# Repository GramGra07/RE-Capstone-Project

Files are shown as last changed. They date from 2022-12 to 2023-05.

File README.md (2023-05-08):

# Programmable, Autonomous Car
## Zale Diawara and Graden Gentry
## 5/6/23

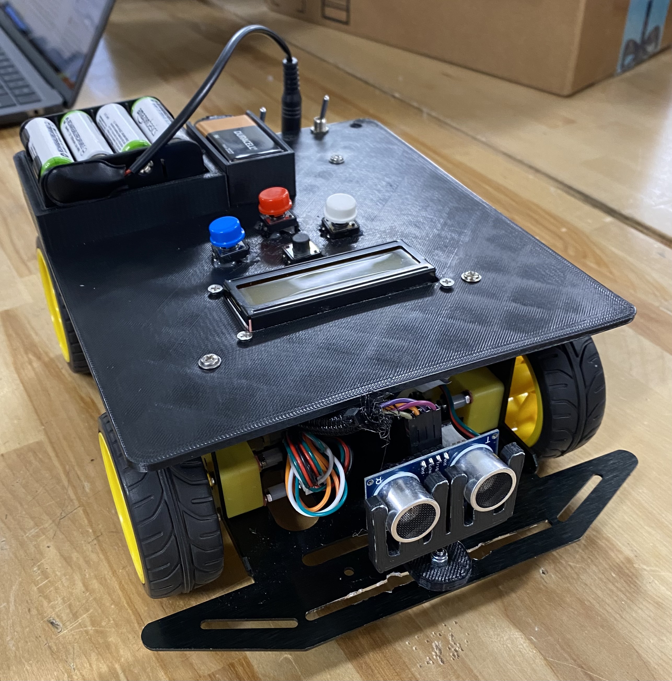
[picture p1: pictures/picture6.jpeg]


 ## Design Summary

We have made a robotic car that will allow a user to set direction and distance instructions for the robot to follow. For instance, the user will start the car and the LCD display will ask for a direction which will be input using one of the three buttons ( black, white, blue). It will then put the current selection on the LCD display. If the user is satisfied with their selection, they will tap the red button to accept the response and it will move on to selecting a distance. A base distance will be already selected and the user will use the white and blue buttons to change the distance. It will only allow the user to select 0 cm if the user has previously selected a direction of right or left. If the user selects forward, the minimum distance is 20 cm and the maximum is 90 cm. Once the user is again satisfied with the selection they will tap the red button again and it will save the selection. At this point in the program, it will allow the user to do the process again, or run the robot by pressing the red button again. Once running, the car will make sure it doesn’t crash by using a distance sensor to stop it an average of 6 cm away from an object.

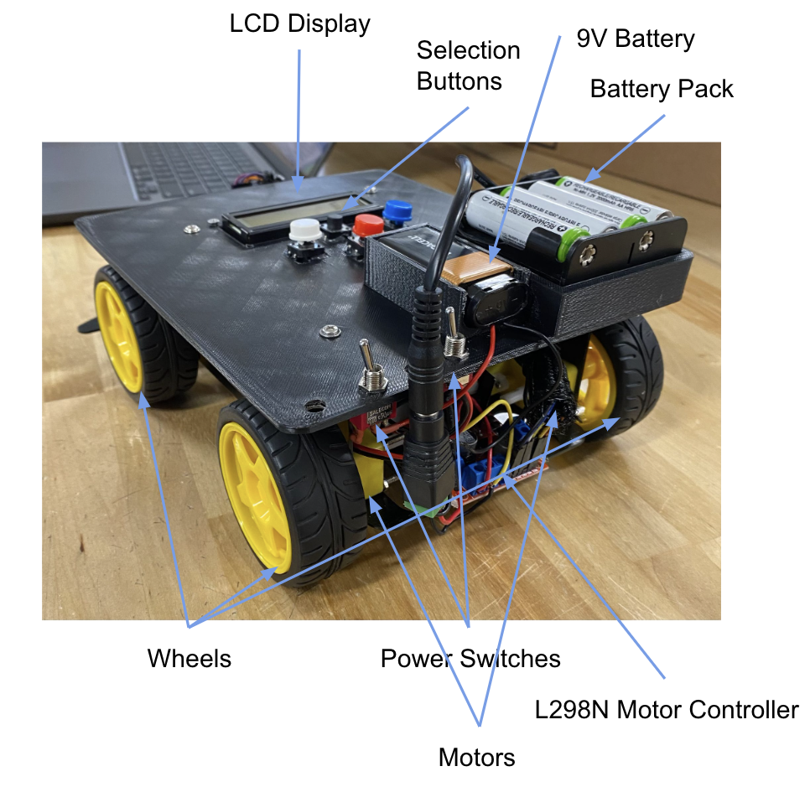
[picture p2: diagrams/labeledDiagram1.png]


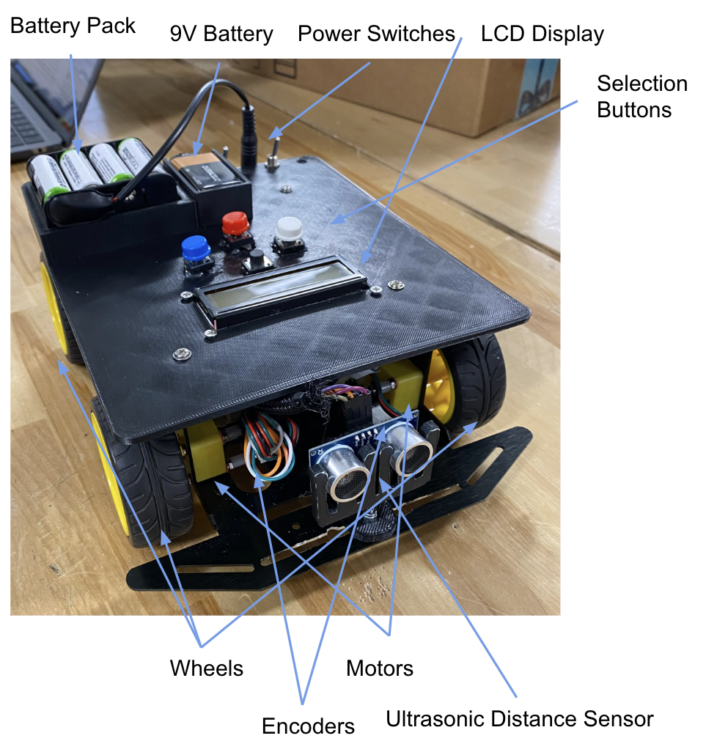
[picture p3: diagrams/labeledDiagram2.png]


## System Details

The robot is using some basic parts like Arduino motors and more complex parts like the Arduino Mega Elegoo. The first element of the robot where everything starts is the Arduino Elegoo because that is where the code is stored and also it is the part that sends those codes to the motors, the buttons and the LCD screen. The Arduino Elegoo Mega is the communicator between the buttons and the motors to transmit the instructions from the buttons to the motors, between the buttons and the LCD screen to display the instructions given from the buttons and finally between the motors (especially the encoders) and the ultrasonic sensor to tell the motors to stop when the robot is too close to hit something (around 6 cm). 
All these parts need power to run. At the beginning we used a battery pack with eight rechargeable small batteries with 1.2V and 2000mAh each to power both the Arduino and motors but we found that it wasn’t enough to power both. Because of this we use eight rechargeable batteries to power the motors, and a 9V battery to power the Arduino  (Figure 3). 
The robot also needs a lot of code in order to run correctly and efficiently. We use two true and false encoders to determine position and are able to count encoder ticks. After the robot is started, the user will allow the robot to calibrate, and manual calibrate if needed, and then will push the red button to start the program. Then they will start creating instructions for the robot by selecting a direction and distance for each step as seen in Figure 2. Our wiring is fairly simple. We have a breadboard in the middle for power and ground that most things are plugged into. Through this, we are able to get many more slots for power and ground and it is easier to distribute power. Most of our wires are organized through zip ties and cable holders. You can see the wiring diagram in Figure 1. There are a lot of wires that we have to manage and contain. We are using a lot of the pins on our Arduino Mega, which was the entire point of getting it. We have put hot glue on most of the connections to the Arduino to make sure they stay connected.
The code is based on functions and is all linear. There is no code in the loop() section that Arduino gives you because this would result in a repetition of the code we want to run only once. To start, it runs the selection code, found in Code Block 1, and then will break out of that once it is told to run. This will repeatedly ask the user for two inputs, a direction and distance until the user decides to run the program. Then, it will run the code to make the motors run until the encoders count to a certain number based on the instructions the user has given. This code is found in Code Block 3. We have also created functions to run the LCD. These are able to cut the message that the LCD will use because the LCD is only 16 characters long. The print function, found in Code Block 2, checks that the message variable is less than the 16 character limit, but if it is more than 16 characters it will cut the message down and make a second message for the second line. We also ran into a problem with the true and false encoders, if one is true and the other is false, the one that is false will go farther than the one that is true. To solve this problem, we calibrate the encoders and motors through the functions in Code Block 4, which contains both automatic and manual calibration options. The automatic function works by making the motors stop when both encoders are false. The manual function will tell the user the current encoder values and finish once both are at the correct position.
We 3D printed two parts, the top of the robot and the 9V battery holder found in Figure 4 and 5 in the appendix. 3D printing was very useful because it allowed us to accurately manufacture parts that we needed. We used the top of the robot print to mount the LCD, buttons, switches, and batteries. We printed the 9V battery holder and attached it to the top of robot part.
There are not many mechanical aspects to this project but we have used the Spartan kit as a base. Our current drivetrain has four Arduino motors mounted to a metal frame from the Spartan kit. Two of these motors have encoder mounts built in. Mostly because it already had everything we needed so we could start testing immediately. There are special mounts for the encoders on the motors, and convenient spots to mount the motors. There are four beams that go straight up to attach the top of the robot to the bottom frame. Inside the frame, there is enough space for the Arduino, motor controller, and motors inside the robot.

## Design Evaluation

While building this robot, we have incorporated a LCD screen as an output display, four buttons for user input, a distance sensor and encoders for autonomous input, four reversible DC motors using a L289N motor driver, and a lot of programmed logic in the software. The programmed logic includes our algorithm that indexes through the variable called actions and tells the robot what to do, found in Code Block 5, and our logic that instructs the robot to run the LCD screen. Refer to Code Block 2 for more details on running the LCD screen. We have made every effort to make sure every connection is solid by hot gluing and soldering the wires and that there are no exposed wires that could cause harm. We have two switches that control power to the motors and the Arduino. If either switch is flipped off while the robot is driving, it will stop. Our cost was around $70, mostly used by the Arduino Spartan kit we used as our base. We chose this because it has pre-made slots for encoders and was extremely convenient to use. In addition, $20 was used on the Elegoo Arduino Mega, which has more digital pins than the regular Arduino Uno. We have used around 110 grams of filament. We have 3D printed a top to the robot and a 9V battery holder. This was very useful because it provides slots for the LCD, buttons, and batteries that can be accessed from the top of the robot. All components in our robot serve a defined purpose that is vital to the robot running correctly and accurately. We use one Elegoo Arduino Mega as our controller for this project, powered directly by a 9V battery. We also use a L298N motor controller powered by a 12V battery pack. In the beginning of this project, we knew hitting the early bird deadline was a must so we made it a priority to get most, if not all of the robot done by that date. We think the effort level for this project is actually fairly high as we used true and false encoders to count ticks, as well as a lot of trouble with making sure the lists are created and indexed correctly. 

## Complete Parts List

[Elegoo Arduino Mega][mega]
Part Num: LYSB01H4ZDYCE-ELECTRNCS - Arduino microcontroller - $20

[L298N Motor Controller][mcontroller]
Part Num: CECOMINOD012186m - Used to control all the motors and direction - $2

Arduino Spartan Kit  - Contains a base, four motors, two encoders - $50

[Ultrasonic Distance Sensor HC-SR04][dist]
Part Num: Dana-YJ171306 - $2

[4x Micro Switch Push Button][button]
Part Num: CYT1009 - $4

[AdaFruit Tiny Breadboard][bread]
Part Num: B071KCZZ4K - $4

[LCD Screen][lcd]
Part Num: HD44780 - $4

[4x 220 ohm resistor][resist]
Part Num: EFR-W0D50-A:MF - $0.06

[10k ohm potentiometer][potent]
Part Num: Breadboard trim kit - $4

[8 AA Battery Holder][connector]
Part Num: B07WP1CYYW - $4

[8x AA Battery][aaBat]
Part Num: DURACELL - 04343 - 12/PACK - $16

[9V Battery][batLink]
Part Num: MN1604B1Z - $7

## Lessons Learned

Some of the main issues we faced were in the wiring, the programming of the robot, and the true and false encoders. The robot is very compact and tight, which made it a challenge to organize and plug in wires, especially the buttons as they all had to go in at the same time. Although we got off to a quick start with the programming, it was a challenge to learn more about how Arduino char type variables work and how to take a specific value out of that correctly. We fixed this by taking the original value and subtracting the ASCII value of 0, our starting number. We also learned more about how adding characters to the end of a string works. This was a little bit of a challenge because we weren’t able to just add the character to the end of the string and we ended up having to replace the very end character in order to make it work better. You can see this in Code Block 1 in the appendix, where we take the message’s length, and then replace the end character ( a space ), with the selected character. We would recommend that other students try to keep all variables in the same format so you don't run into any errors trying to convert between types, specifically ASCII characters and strings, which are easy to fix, but confusing to understand and debug. We would also recommend intensive use of the serial monitor for Arduino, and print statements for python, it makes it super easy to find breakpoints and easily debug the code. True and false encoders have also been a problem through this project. If one starts as “on”, and the other encoder starts as “off”, then when it counts, it will have to go further for the one that started as “off”. We made a calibration sequence to combat this problem, and by running the motors until both encoders reach an “off” state, we can get more accurate movements as seen in Code Block 4 in the appendix.

## How to Build It

You will need a Spartan Kit, four buttons, an Arduino Mega, 4 220 ohm resistors, 1 10k ohm potentiometer, a tiny breadboard, a lot of wires, an LCD screen, the Top of Robot 3D print, 12V battery pack, 9V battery and holder 3D print, a Ultrasonic Distance sensor, and a L298N motor controller.

1. Take the top part off the spartan robot which will be later replaced with the 3D print.



2. Assemble the LCD screen to the Arduino based on the wiring diagram and as seen at this link.

3. Assemble the power and ground board for the robot. This is done by having one side of the tiny breadboard for power, and the other for ground. Then all wires will be connected to this breadboard for power and ground. This is used for power distribution through the entire system. The wiring is shown in the wiring diagram.

4. Solder the switches into the power source wires. These switches act as a break in the wire so when it is on, it will allow flow through the wire. Cut the power wire in half and connect one of the halves to the middle pin and the other half to one of the outside pins on the switch. When it is off, the switch will be on the same side as the wire on the outside pin. The red wire from the power connector will be connected to the 12V pin on the motor controller, and the black ground wire from the power connector and the gnd from the Arduino will both be connected to the gnd pin on the motor controller.

5. You will then connect the motor driver to the Arduino Mega and motors as shown in the wiring diagram, 2 motors will be connected to each side of the motor driver.

6. You will then need to solder wires to the ends of the buttons as shown in the wiring diagram. One pin will be connected to power, the others to the ground and pin on the Arduino. The bottom right pin goes to ground, the top right pin to power through a resistor, and the top left pin to the Arduino for input.

7. You will then connect the distance sensor as shown in the wiring diagram. And insert it into the distance sensor holder, found in our repository under CAD.

8. Put on the top of the robot while connecting the buttons through the holes in the 3D print, and mounting the switches, as well as screwing in the LCD screen.

9. Screw in the top of the robot print to the metal frame.

## Appendix

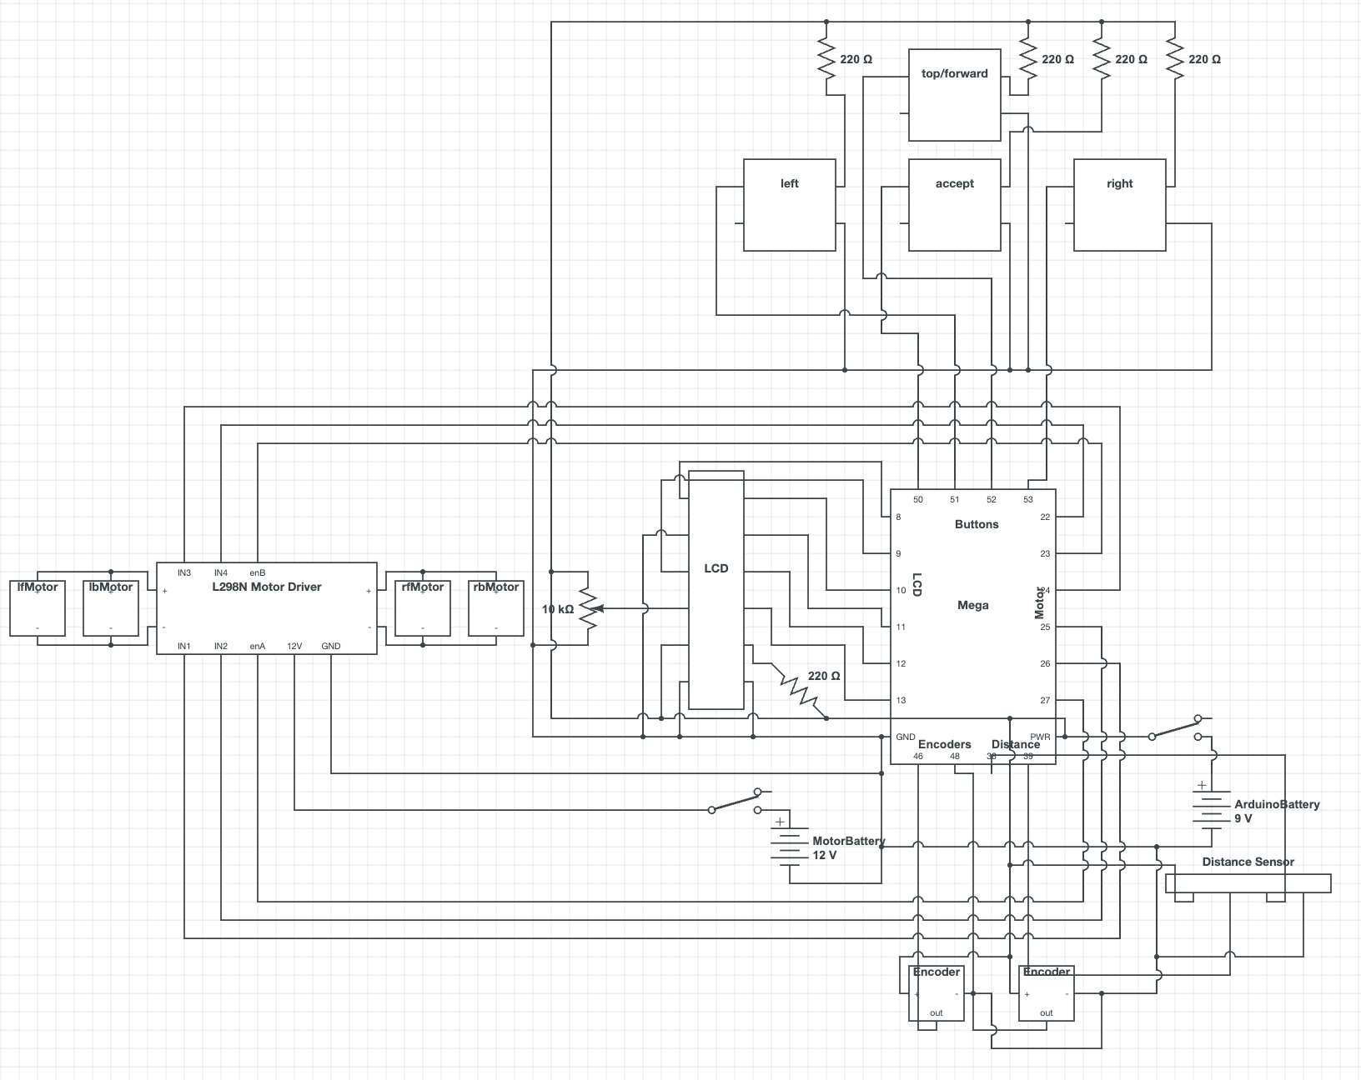
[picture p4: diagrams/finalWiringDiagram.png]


Figure 1 (Circuit Diagram)

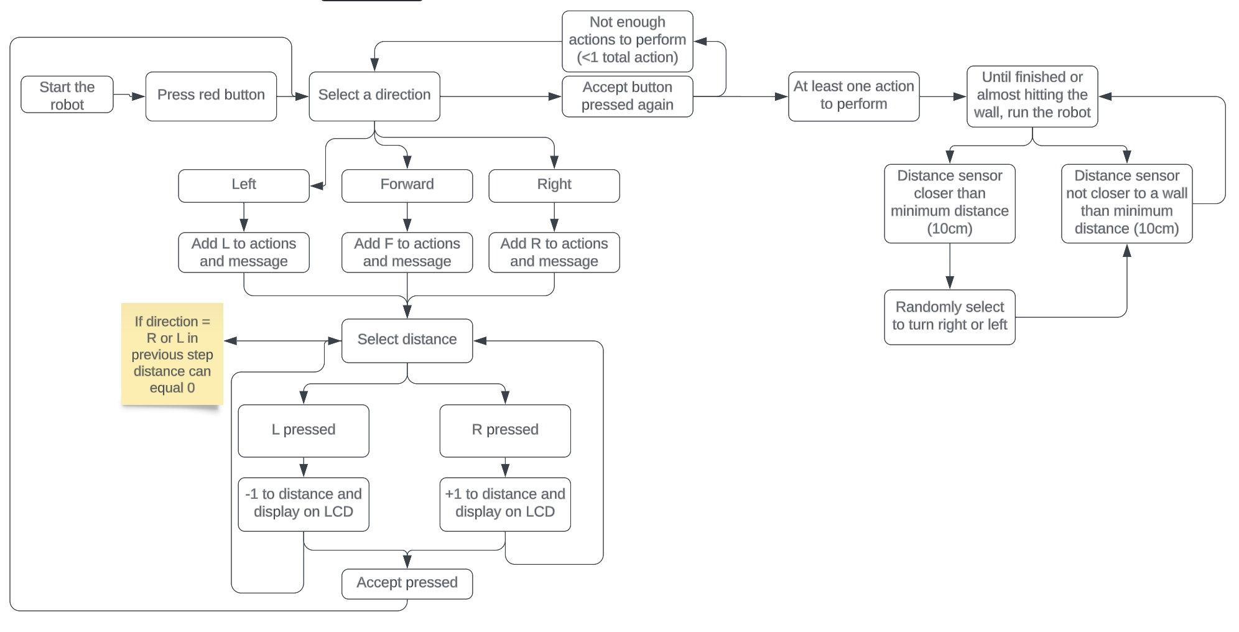
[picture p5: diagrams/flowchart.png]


Figure 2 (Flowchart of the system)

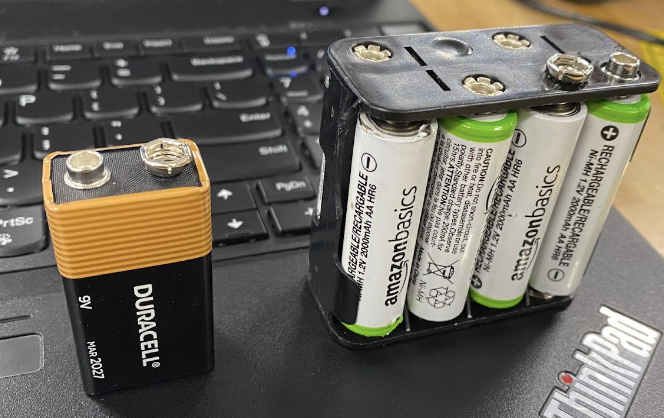
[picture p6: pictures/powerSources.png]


Figure 3 (Power Sources)

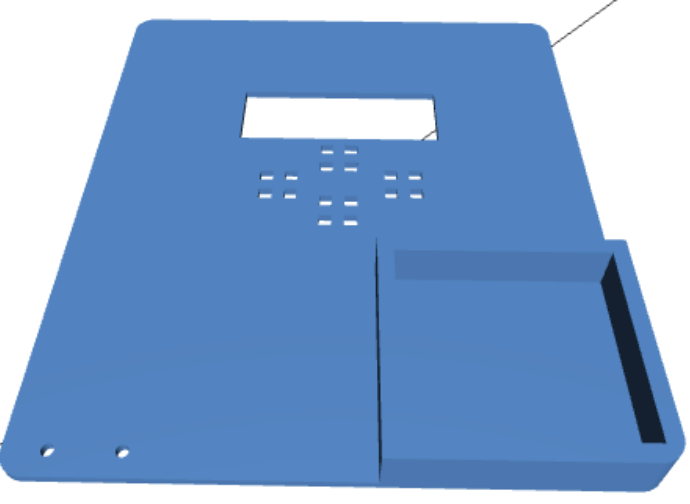
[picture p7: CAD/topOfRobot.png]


Figure 4 (Top of Robot)

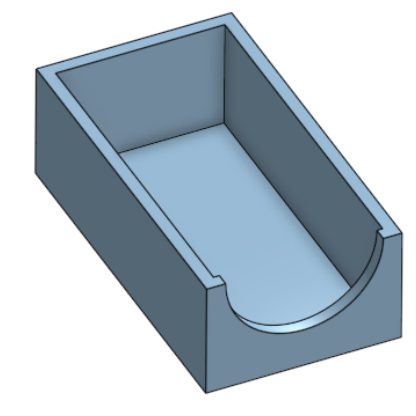
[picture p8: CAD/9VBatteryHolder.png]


Figure 5 (9V Battery Holder)

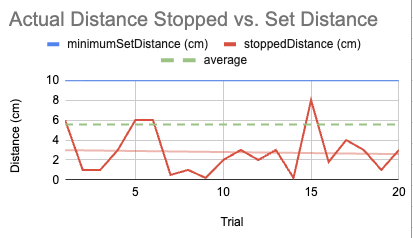
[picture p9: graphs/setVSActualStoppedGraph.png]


Figure 6 (Stopped vs. Minimum Distance Graph)

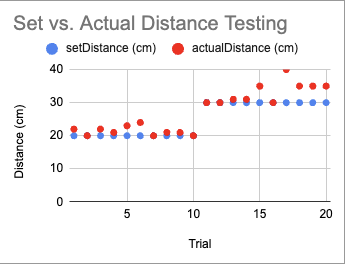
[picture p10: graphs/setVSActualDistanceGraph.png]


Figure 7 (Actual vs. Set Distance Testing Graph)

Code Block 1 (Selection portion of code, will make the custom “code” to run the robot)

```
void doSelections(boolean d, boolean t) {
  while (d and !runOVR) {
    message = "Select direction:  ";  // ask for direction
    if (firstTime) {
      lcd.clear();
      print(15);          //function to alter the string to make it multi-line
      firstTime = false;  //breaks out of running this if again
      ifAdded = false;
      delay(500);
    }
    while (digitalRead(acceptBPin)) {                                                                      //while not accepted
      if (digitalRead(fBpin) and digitalRead(rBpin) and digitalRead(lBpin) and digitalRead(acceptBPin)) {  //checks that all buttons not pressed
        isHigh = false;
      }
      if (!digitalRead(fBpin) and !isHigh) {  // forward has been pressed
        actions[actions.length() - 1] = 'F';//put F at the end
        message[message.length() - 1] = 'F';
        lcd.clear();
        print(15);
        ifAdded = true;
      }
      if (!digitalRead(rBpin) and !isHigh) {  //right has been pressed
        actions[actions.length() - 1] = 'R'; //put R at the end
        message[message.length() - 1] = 'R';
        lcd.clear();
        print(15);
        ifAdded = true;
      }
      if (!digitalRead(lBpin) and !isHigh) {
        actions[actions.length() - 1] = 'L'; //put L at the end
        message[message.length() - 1] = 'L';
        lcd.clear();
        print(15);
        ifAdded = true;
      }
      if (!digitalRead(acceptBPin) and message[message.length() - 1] == ' ' and !isHigh and actions.length() > 1) {
        // above will check that first, accept is pressed, second, that the last character is a space, third, that isHigh is false, and fourth, that actions is greater than 1
        t = false;
        d = false;
        runOVR = true;
        resetLCD();
        indexIntoActions();
        return;
      } else if (!digitalRead(acceptBPin) and !isHigh and ifAdded) {
        actions += ' ';  //adds blank space to indicate next is empty
        resetLCD();
        firstTime = true;
        doSelections(false, true);  //switch selection to distance
      }
    }
  }
  while (t and !runOVR) {
    dist = begindist;               //automatically selects beginDist as a distance
    message = "Select distance (l=-,r=+):  " + String(dist) + "0";  //print out on the lcd
    if (firstTime) {
      lcd.clear();
      print(16);
      firstTime = false;
      delay(500);
    }
    while (digitalRead(acceptBPin)) {                   //not accepted
      delay(100);
      if (digitalRead(rBpin) and digitalRead(lBpin)) {  //makes sure none was pressed
        isHigh = false;
      }
      if (!digitalRead(rBpin) and !isHigh) {  //pressed up/right
        if (dist < 9) {
          dist++;  //increase if less than nine
          if (dist == 1){
            dist++;
          }
        }
        lcd.clear();
        String tl = String(dist);
        message[message.length() - 2] = tl[0];
        print(16);  //prints out new distance
        isHigh = true;
      }
      if (!digitalRead(lBpin) and !isHigh) {  //left/- pressed
        if (dist > 2 and actions[actions.length() - 2] == 'F'){
          dist --;
        }
        if (dist > 0 and (actions[actions.length() - 2] == 'R' or actions[actions.length() - 2] == 'L')) {
          dist--;
          if (dist == 1){
            dist --;
          }
        }
        lcd.clear();
        String tl = String(dist);
        message[message.length() - 2] = tl[0];
        print(16);  //show new message
        isHigh = true;
      }
      if (!digitalRead(acceptBPin)) {  //has been accepted
        String tl = String(dist);
        actions[actions.length() - 1] = tl[0];  //add it to actions
        actions += ' ';
        Serial.println(actions);
        resetLCD();
        firstTime = true;
        doSelections(true, false);  //switch selection
      }
    }
  }
}
```

Code Block 2 (Print function for the LCD, will cut strings at whatever characters you want to)

```
void print(int start) {  //start will usually be 16 but changed to make not cut off words
 if (message.length() >= 16) { //if message is longer than 16
   makeMessage(0, start);         //make a message only through start variable
   lcd.print(m);                  //prints first line
   x = message.length() - start;  //changes line
   y = 1;                         //next line
   lcd.setCursor(0, 1);// set new cursor
   makeMessage(start, message.length());  //make a latter half message
   lcd.print(m);                          //print it out
 } else { //if message is less than 16
   lcd.print(message);  //will print the message
 }
}
void makeMessage(int s, int e) { //will make a message from s to e
 m = "";
 for (int i = s; i < e; i++) {
   m += message[i];
 }
}
```

Code Block 3 (Run to Position with Encoders)

```
int counter = 1;
void runToPosition(double r, double l, int mult) {//mult = 2 for forward, 8 for turning
  if (not hasRun) {
    resetEncoders();
    r *= -countsPerCM;
    l *= -countsPerCM;
    r *= mult;
    l *= mult;
    if (r < 1) {
      r *= -1;
      rRunF = false;
    }
    if (l < 1) {
      l *= -1;
      lRunF = false;
    }
    r = round(r);
    l = round(l);
  }
  while ((rCPose < r or lCPose < l) and not finished) {
    if (counter == 1) {  // only set power once
      if (lRunF) {       //if running forward
        digitalWrite(in1, HIGH);
        digitalWrite(in2, LOW);
      } else {  //running backward
        digitalWrite(in1, LOW);
        digitalWrite(in2, HIGH);
      }
      if (rRunF) {  //running forward
        digitalWrite(in3, HIGH);
        digitalWrite(in4, LOW);
      } else {  //backwards
        digitalWrite(in3, LOW);
        digitalWrite(in4, HIGH);
      }
    }
    rCPose = int(rCPose);
    lCPose = int(lCPose);
    analogWrite(enA, speed);  //set it to speed
    analogWrite(enB, speed);
    //both to position, stop and reset
    if (lCPose >= l and rCPose >= r) {
      resetLCD();
      message = "Done!";
      print(12);
      stopMotors();
      finished = true;
      resetEncoders();
      calibrate();
      break;
    }
    //is already counted
    if (digitalRead(lEpin) == 0 and !isHighL) {
      isHighL = true;
      lCPose += 1;
    } else if (digitalRead(lEpin) == 1) {  //was counted, be ready to count again
      isHighL = false;
    }
    //check if its counted
    if (digitalRead(rEpin) == 0 and !isHighR) {
      isHighR = true;
      rCPose += 1;
    } else if (digitalRead(rEpin) == 1) {  // was counted as a one
      isHighR = false;
    }
    //if it has gone to far, stop
    if (lCPose >= l) {
      digitalWrite(in1, LOW);
      digitalWrite(in2, LOW);
    }
    if (rCPose >= r) {
      digitalWrite(in3, LOW);
      digitalWrite(in4, LOW);
    }
    //stop for distance
    if (getDistance() <= minimumDist and getDistance() <= minimumDist and getDistance() <= minimumDist) {
      stopMotors();
      finished = true;
      resetEncoders();
      resetLCD();
      message = "Stopped for distance < " + String(minimumDist) + " cm";// print out message
      print(12);
      runAway();
      break;
    }
    counter += 1;
  }
}
```

Code Block 4 (Calibration Sequences)

```
void calibrate(){
  resetLCD();
  message = "Please wait for calibration";
  print(16);
  delay(500);
  analogWrite(enA, 150);  
  analogWrite(enB, 150);
  while  (not digitalRead(lEpin) == 0 or not digitalRead(rEpin) == 0){
    if (digitalRead(lEpin) == 1){
      digitalWrite(in1, HIGH);
      digitalWrite(in2, LOW);
    }
    if (digitalRead(lEpin) == 0){
      digitalWrite(in1, LOW);
      digitalWrite(in2, LOW);
    }
    if (digitalRead(rEpin) == 1){
      digitalWrite(in3, HIGH);
      digitalWrite(in4, LOW);
    }
    if (digitalRead(rEpin) == 0){
      digitalWrite(in3, LOW);
      digitalWrite(in4, LOW);
    }
    if (digitalRead(lEpin) == 0 and digitalRead(rEpin) == 0){
      digitalWrite(in1, LOW);
      digitalWrite(in2, LOW);
      digitalWrite(in3, LOW);
      digitalWrite(in4, LOW);
      resetLCD();
      message="Calibration complete!";
      print(12);
      delay(500);
      break;
    }
  }
}
void manualCalibrate(){
  stopMotors();
  bool lCalibrated = false;
  bool rCalibrated = false;
  resetLCD();
  message = "Manual calibration required";
  print(16);
  delay(2000);
  resetLCD();
  message = "Please turn the front two wheels";
  print(16);
  delay(2000);
  resetLCD();
  message = "Complete:   ";
  print(16);
  if (digitalRead(lEpin) == 0 and digitalRead(rEpin) == 0){
    delay(500);
    resetLCD();
    message="Calibration complete!";
    print(12);
    delay(500);
  }
  while (digitalRead(lEpin) == 1 or digitalRead(rEpin) == 1){
    if (digitalRead(lEpin) == 0 and not lCalibrated){
      lcd.clear();
      message[message.length() - 2] = 'L';
      print(16);
      lCalibrated = true;
    }
    if (digitalRead(lEpin) == 1 and lCalibrated){
      lcd.clear();
      message[message.length() - 2] = ' ';
      print(16);
      lCalibrated = false;
    }
    if (digitalRead(rEpin) == 0 and not rCalibrated){
      lcd.clear();
      message[message.length() - 1] = 'R';
      print(16);
      rCalibrated = true;
    }
    if (digitalRead(rEpin) == 1 and rCalibrated){
      lcd.clear();
      message[message.length() - 1] = ' ';
      print(16);
      rCalibrated = false;
    }
    if (digitalRead(lEpin) == 0 and digitalRead(rEpin) == 0){
      resetLCD();
      message="Calibration complete!";
      print(12);
      delay(500);
      break;
    }
  }
}
```

Code Block 5 (Index into Actions)

```
void indexIntoActions() {
  Serial.println("Running with " + actions);//tell computer it is running
  lcd.noCursor();
  message = "Running, watch out!";//warn user
  print(15);
  delay(2500);
  resetLCD();
  message = actions;
  print(16);
  actions.replace(" ", "");
  for (int i = 0; i < actions.length(); i += 2) {
    d = int(actions[i + 1]) - 48; //converts to int from ascii
    d *= 10;
    if (d == -480) { // this case should never happen but it is here in case
      d += 480;
    }
    dir = String(actions[i]);// finds direction
    if (dir == "R") { //if right
      turnRight();
    } else if (dir == "L") { //if left
      turnLeft();
    }
    if (d != 0) { //if distance is not 0, aka it won't move
      delay(500);
      runToPosition(d, d,4); //run to position
    }
  }
}
```

[batLink]: https://www.amazon.com/Duracell-Coppertop-Alkaline-Batteries-Count/dp/B00009V2QT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

[aaBat]: https://www.amazon.com/dp/B006D0U9IO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

[connector]: https://www.amazon.com/Thicken-Battery-Holder-Standard-Connector/dp/B07WP1CYYW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

[resist]: https://www.amazon.com/EDGELEC-Resistor-Tolerance-Multiple-Resistance/dp/B07QK9ZBVZ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

[lcd]: https://www.amazon.com/HiLetgo-Display-Backlight-Controller-Character/dp/B00HJ6AFW6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

[bread]: https://www.amazon.com/HiLetgo-SYB-170-Breadboard-Colorful-Plates/dp/B071KCZZ4K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

[button]: https://www.amazon.com/Cylewet-12x12x7-3mm-Momentary-Tactile-Arduino/dp/B01NCQVGLC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

[dist]: https://www.amazon.com/HiLetgo-HC-SR04-Ultrasonic-Distance-MEGA2560/dp/B00E87VXH0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

[mcontroller]: https://www.amazon.com/dp/B014KMHSW6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

[mega]: https://www.amazon.com/ELEGOO-ATmega2560-ATMEGA16U2-Arduino-Compliant/dp/B01H4ZDYCE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

[potent]: https://www.amazon.com/MCIGICM-Breadboard-Trim-Potentiometer-Arduino/dp/B07S69443J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

[instruct]: https://docs.arduino.cc/learn/electronics/lcd-displays

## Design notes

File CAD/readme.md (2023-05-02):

# CAD Links to OnShape and Thingiverse

https://www.thingiverse.com/thing:2592461

https://cad.onshape.com/documents/cad8327a4a89d74d30c004e5/w/d4d6bca20e19bab73086496e/e/89a1af89d654e21385c83372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

https://cad.onshape.com/documents/13337cf7825cb6f3414f7f88/w/0d906049e6c0f16e8b8ad14b/e/1b3ed14cf75f743408db7ab0

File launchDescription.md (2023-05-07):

# RE-Capstone-Project
# A Completely Autonomous, Programmable Car with Four Button Controls
## By Graden Gentry and Zale Diawara

# Launch Description

## Project Description
We have built a robot that will be able to be programmed by a person as to which direction, and how far in that direction. The user will press buttons to select steps, after this, they will hit the accept button again to execute the steps. It takes input from a distance sensor to make sure it won't crash into something. It shows output back to the user with an LCD screen. There are two battery packs, one 9V battery for the Arduino, and one 12V battery for the motors. There are two power switches and they each must be on for the robot to function. It has a distance sensor in the front and will stop if anything is closer than 10 cm, then it will print out that it has stopped on the LCD screen.

## Looks:
It will look like a car with 4 wheels, and we will try to make it as polished as possible.
It will have four different colored buttons on the top as well as an LCD screen embeded into the top.

## Basis for this project
We wanted to do this project based on the idea of programming a user input, and translating it into robot movements.
We use a certain code, like F6R9L0F8, and translate that into how the robot will move. In that case, Forward 60, Right turn and then Forward 90, Left turn and Forward 0, then finally Forward 80. The main idea is to create our own code, and then read through it and perform those programmed actions.

## Cost Overview

Arduino Mega Elegoo $20

Arduino OLD Spartan kit $50

Total $70

Total Filament Used: 110 g

## Useful Links
https://create.arduino.cc/projecthub/ishaq-yang/auto-ultrasonic-car-a85c6f

https://www.hackster.io/ronfrtek/how-to-make-arduino-obstacle-avoiding-robot-car-with-radar-1d4a3b

https://core-electronics.com.au/guides/use-lcd-arduino-uno/ and https://docs.arduino.cc/learn/electronics/lcd-displays

Capstone instructions: https://docs.google.com/document/d/1Ap9XnDHmlUpDhtRLOVqSsqf3xh5cZPlc8qJfAl380MQ/edit

Our Poster: https://docs.google.com/presentation/d/13sadksnsIwi6zoIYFUSCJ5H2SOaSJQ3OA5F7KWZk8_I/edit?usp=sharing

Testing Log: https://docs.google.com/spreadsheets/d/1tO00ziJ-Gukyq96_y4_CSVAVIG8Ud_WrxS_RcOtxezU/edit#gid=0

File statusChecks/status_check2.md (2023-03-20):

1. Code is located in the code and encoder folders
2. Some resources we have used is the internet to learn about distance sensors and motor drivers, and to look for parts we might need online as well as the prices of several things.
3. We think that the only thing that needs to be manufactured is the final top of the robot, which will mount the lcd and buttons

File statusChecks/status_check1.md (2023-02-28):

1. We have begun constructing a protoptye to test the code on, we have begun to code and test the code, and we started to Cad the system.
2. We do not need to order anything.
3. We have started to cad the chassis but have not finished as we want to have a somewhat finished product, and then build around it.
4. Our output display is an LCD screen, user input is buttons that select the direction and time, our autonomous input is a distance sensor, our actuators are motors, and our miscelaneous materials include programmed logic, menu software, and data storage and retrieval.
5. The three most challenging parts of this project will be finishing the code, cad-ing the car chassis, cad-ing the slots and spaces for everything.

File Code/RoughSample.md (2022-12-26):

#include <LiquidCrystal.h>
const int rs = 12, en = 11, d4 = 5, d5 = 4, d6 = 3, d7 = 2;
LiquidCrystal lcd(rs, en, d4, d5, d6, d7);
char message[]="hello worldyybyy opp";
int y = 0;
int x = sizeof(message);
String m ="";

void setup() {
  Serial.begin(9600);
  lcd.begin(16, 2);
  print();
}

void loop() {
  lcd.cursor();
  lcd.setCursor(x, y);
}
void print(){
  if (sizeof(message)>=16){
    x=0+sizeof(message)-16;
    y=1;
    makeMessage(0,16);
    Serial.println(m);
    delay(5000);
    makeMessage(16,sizeof(message));
    Serial.println(m);
  }
  lcd.print(message);
}
void makeMessage(int start, int end){
  m ="";
  for (int i = start; i<end;i++){
    m+=message[i];
  }
}

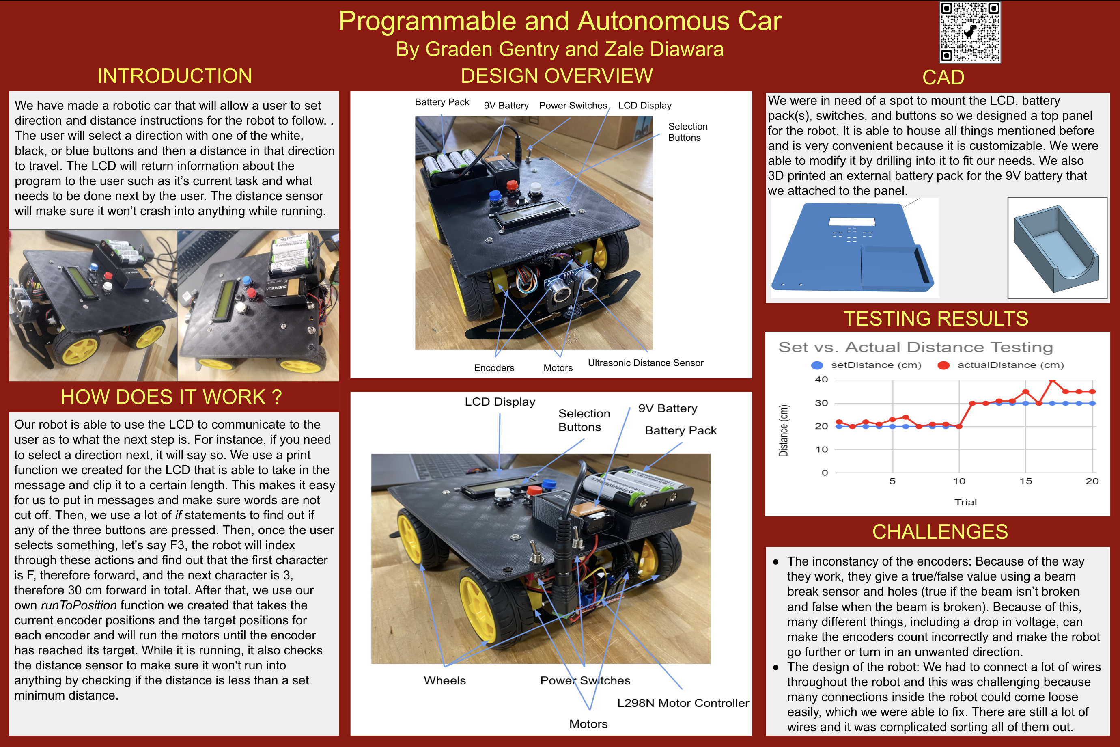
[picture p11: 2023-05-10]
poster.png

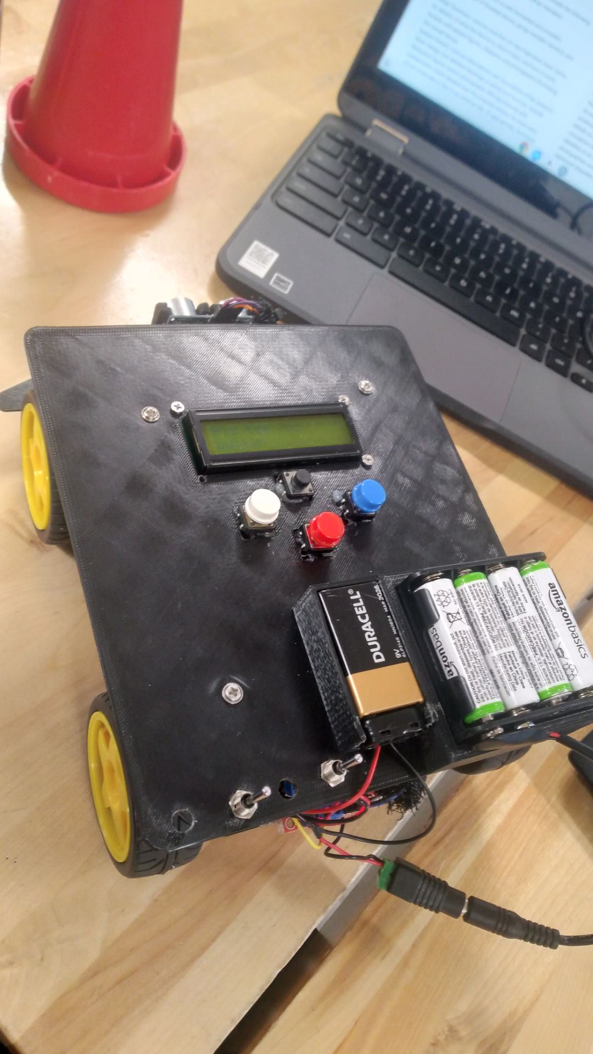
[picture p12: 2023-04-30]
pictures/picture4.jpeg

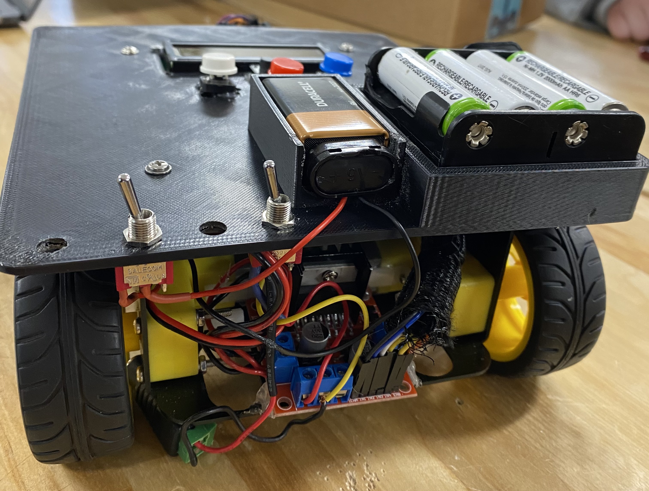
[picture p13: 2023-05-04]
pictures/picture7.jpeg

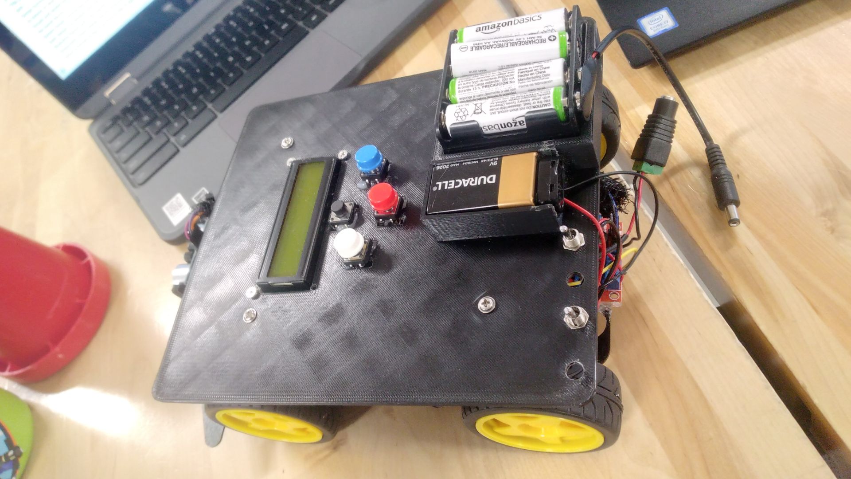
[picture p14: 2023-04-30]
pictures/picture2.jpeg

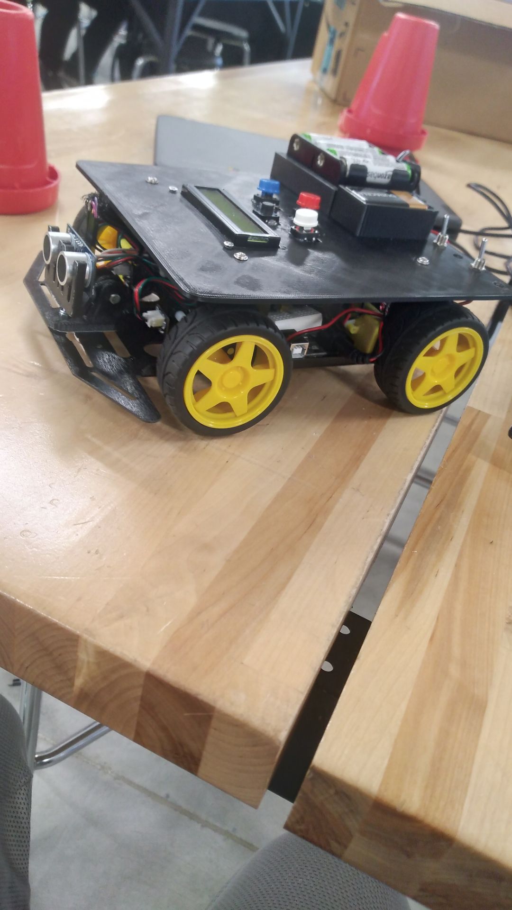
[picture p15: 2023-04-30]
pictures/picture1.jpeg

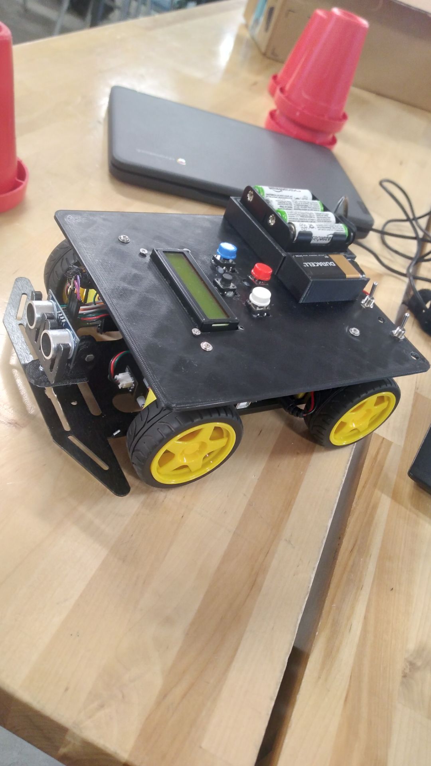
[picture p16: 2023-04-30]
pictures/picture3.jpeg

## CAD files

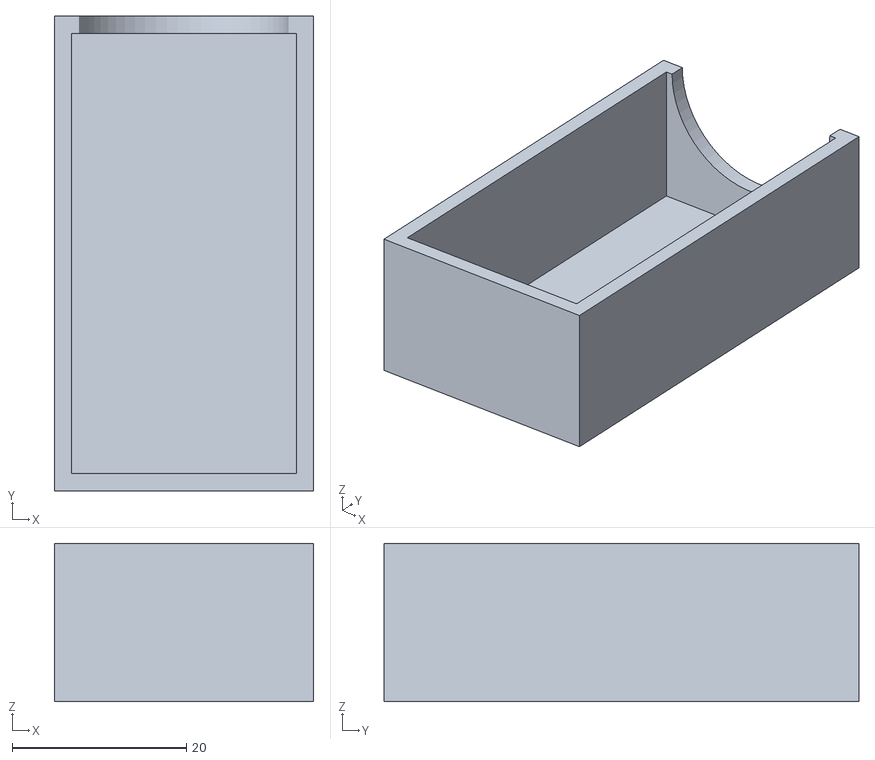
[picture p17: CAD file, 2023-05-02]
CAD/9V_batteryHolder.stl
29.8 x 54.6 x 18.2

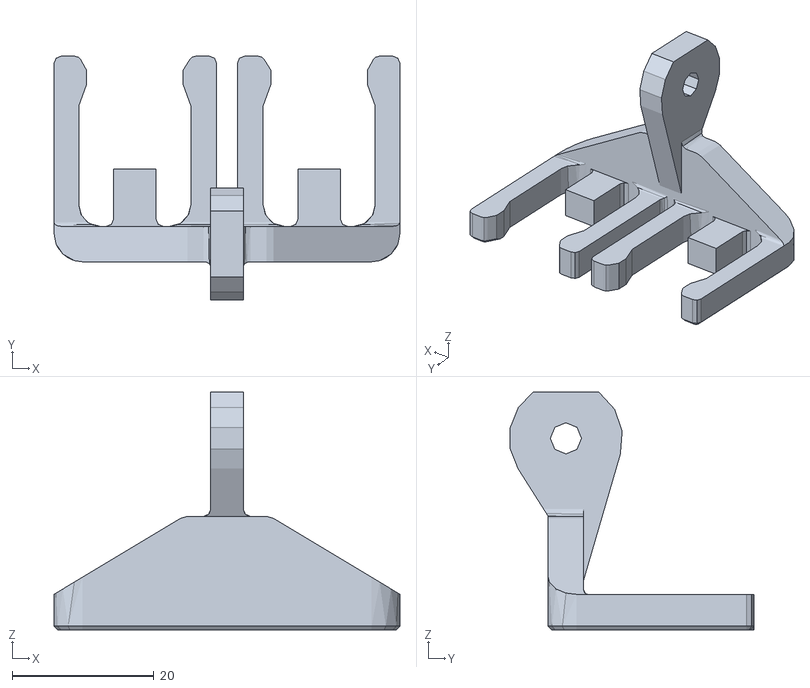
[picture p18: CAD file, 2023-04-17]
CAD/distanceSensorMount/Art_2_HCSR04_b (1).stl
48.8 x 34.4 x 33.5

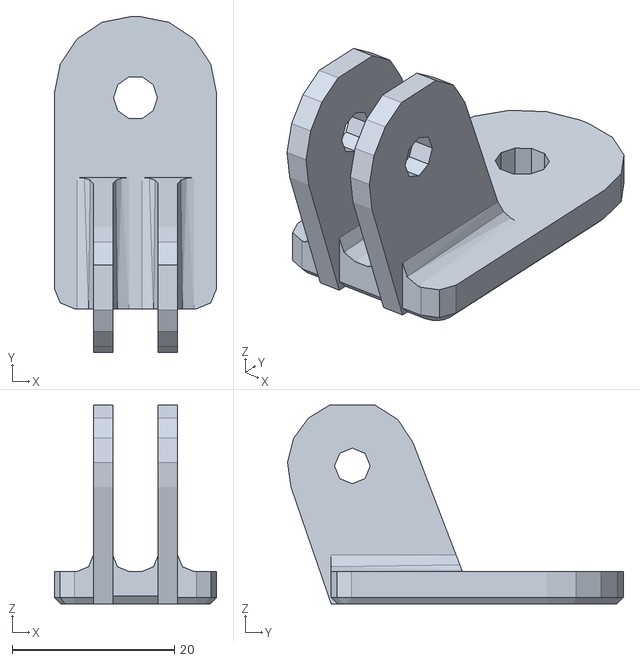
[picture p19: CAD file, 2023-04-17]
CAD/distanceSensorMount/Art_1_HCSR04_b.stl
20.0 x 41.4 x 24.5

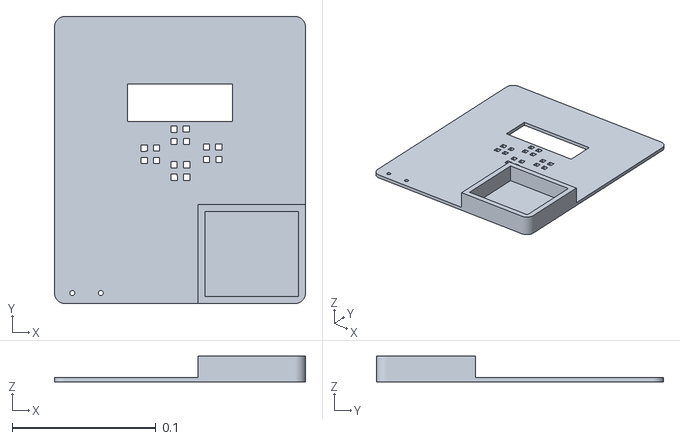
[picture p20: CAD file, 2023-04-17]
CAD/Top_of_Robot.stl
0.175 x 0.2 x 0.018

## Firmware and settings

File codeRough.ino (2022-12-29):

//lcd
#include <LiquidCrystal.h>
const int rs = 13, en = 12, d4 = 11, d5 = 10, d6 = 9, d7 = 8;
LiquidCrystal lcd(rs, en, d4, d5, d6, d7);
String message = "Plz tap center button";
int y = 0;
int x = message.length() - 1;
int t = 0;
String m = "";
String actions = "";
//button
const int acceptBPin = 7, fBpin = 6, rBpin = 5, lBpin = 4;// using 7-4 as inputs
int aBS = 0, fBS = 0, bBS = 0, rBS = 0, lBS = 0; //button states
const int motorBR = 3, motorBL = 2, motorFR = 1, motorFL = 0;
//other
boolean isStarted = false;
boolean directionS = false;
boolean lengthS = false;
boolean accepted = false;
boolean runOVR = false;
boolean hasRun = false;
//Serial.println(message.length());
void setup() {
  pinMode(acceptBPin, INPUT);
  pinMode(fBpin, INPUT);
  pinMode(rBpin, INPUT);
  pinMode(lBpin, INPUT);
  Serial.begin(9600);
  lcd.begin(16, 2);
  print(15);//starting message
}
void loop() {
  setupButton();
  lcd.cursor();
  if (not isStarted) {
    if (aBS == HIGH) {
      isStarted = true;
      directionS = true;
    }
  }
  while (isStarted) {
    doSelections(directionS, lengthS);
  }
  //Serial.println(actions);
}
void resetLCD() {
  x = 0;
  y = 0;
  lcd.setCursor(x, y);
  lcd.clear();
  message = "";
}
void setupButton() {
  aBS = digitalRead(acceptBPin);
  fBS = digitalRead(fBpin);
  rBS = digitalRead(rBpin);
  lBS = digitalRead(lBpin);
}
boolean isAccepted() {
  int a = digitalRead(acceptBPin);
  while (a != HIGH) {
    //not pressed
    a = digitalRead(acceptBPin);
    if (a == HIGH) {
      return true;
      break;
    }
  }
}
void switchToL() {
  lengthS = true;
  directionS = false;
}
void switchToD() {
  directionS = true;
  lengthS = false;
}
void reBind() {
  int a = digitalRead(acceptBPin);
  int f = digitalRead(fBpin);
  int r = digitalRead(rBpin);
  int l = digitalRead(lBpin);
}
void doSelections(boolean d, boolean t) {
  hasRun = false;
  if (d) {
    resetLCD();
    message = "Select direction:  "; //last = [18]
    print(15);
    int a = digitalRead(acceptBPin);
    int f = digitalRead(fBpin);
    int r = digitalRead(rBpin);
    int l = digitalRead(lBpin);
    while (!isAccepted and not hasRun) {
      if (f == HIGH) {
        actions += "F";
        message[17] = "F";
        lcd.clear();
        print(15);
        if (isAccepted) {
          switchToL();
          hasRun = true;
          break;
        }
      }
      if (r == HIGH) {
        actions += "R";
        message += " R";
        lcd.clear();
        print(15);
        if (isAccepted) {
          switchToL();
          hasRun = true;
          break;
        }
      }
      if (l == HIGH) {
        actions += "L";
        message += " L";
        lcd.clear();
        print(15);
        if (isAccepted) {
          switchToL();
          hasRun = true;
          break;
        }
      }
    }
  }
  if (t) {
    t = 0;
    int a = digitalRead(acceptBPin);
    int f = digitalRead(fBpin);
    int r = digitalRead(rBpin);
    int l = digitalRead(lBpin);
    resetLCD();
    message = "Select time (r = +, l = -): ";
    print(15);
    while (!isAccepted) {
      if (r) {
        t += 1;
      }
      if (l) {
        if (t > 1) {
          t -= 1;
        }
      }
      message += t;
      lcd.print(message);
      if (isAccepted) {
        switchToD();
        break;
      }
    }
  }
}
void print(int start) { //start will usually be 16 but changed to make not cut off words
  if (message.length() >= 16) {
    makeMessage(0, start);
    lcd.print(m);
    x = message.length() - start;
    y = 1;
    lcd.setCursor(0, 1);
    makeMessage(start, message.length());
    lcd.print(m);
  } else {
    lcd.print(message);
  }
}
void makeMessage(int s, int e) {
  m = "";
  for (int i = s; i < e; i++) {
    m += message[i];
  }
}
void runMotors(int d, int t) { //distance and time
  //   1
  //2    3
  if (d == 1) {
    //go forward
    delay(t * 1000);
    //stop
  }
  if (d == 2) {
    //turn -90
    //go forward
    delay(t * 1000);
    //stop
  }
  if (d == 3) {
    //turn 90
    //go forward
    delay(t * 1000);
    //stop
  }
}

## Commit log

2023-03-08 fixed distance sensor and incorporated
    [distanceSensor.ino, encoder.ino]
2023-04-15 rearrange and fix names
    [buttonTester.ino, distanceSensor.ino, encoder.ino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]
2023-05-04 Distance corrected and hopefully done
    [main.ino]
